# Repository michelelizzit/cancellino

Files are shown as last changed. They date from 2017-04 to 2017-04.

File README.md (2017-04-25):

# [Cancellino](https://lizzit.it/cancellino) - Open-source active-RFID automatic gate opening system
Raspberry Pi automatic RFID gate opening system with Telegram integration

    README.md
  
    Written by: Michele Lizzit <lizzit.it>, 25 Apr 2017
    Last update: 25 Apr 2017
    Version: 1.0

More informations are available on the project website: https://lizzit.it/cancellino  

## Description of the project
Cancellino is composed of some active tags and a main unit connected to the gate lock, when the main unit detects the presence of a tag in a set range (configurable from a few cm to 10m), it opens the gate.  
Cancellino does not implemet any form of encryption, the tag broadcasts a static key every two seconds, if the key is correct the main unit opens the gate. It was originally designed for applications where the security of the gate is not a concern (in my case the gate is 1m high, and can be easily opened with a piece of plastic).  
The main unit is composed of a Raspberry Pi connected to the gate lock and to an nRF24L01+ wireless module.  
Each tag is composed of a battery (CR2032), an MCU (Atmega328), and an nRF24L01+ wireless module.  

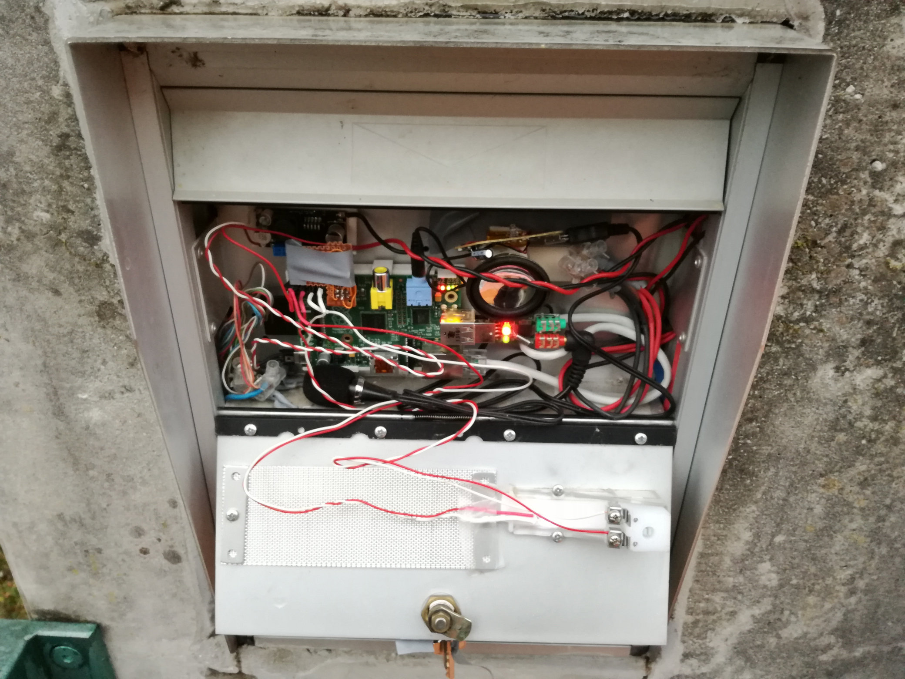
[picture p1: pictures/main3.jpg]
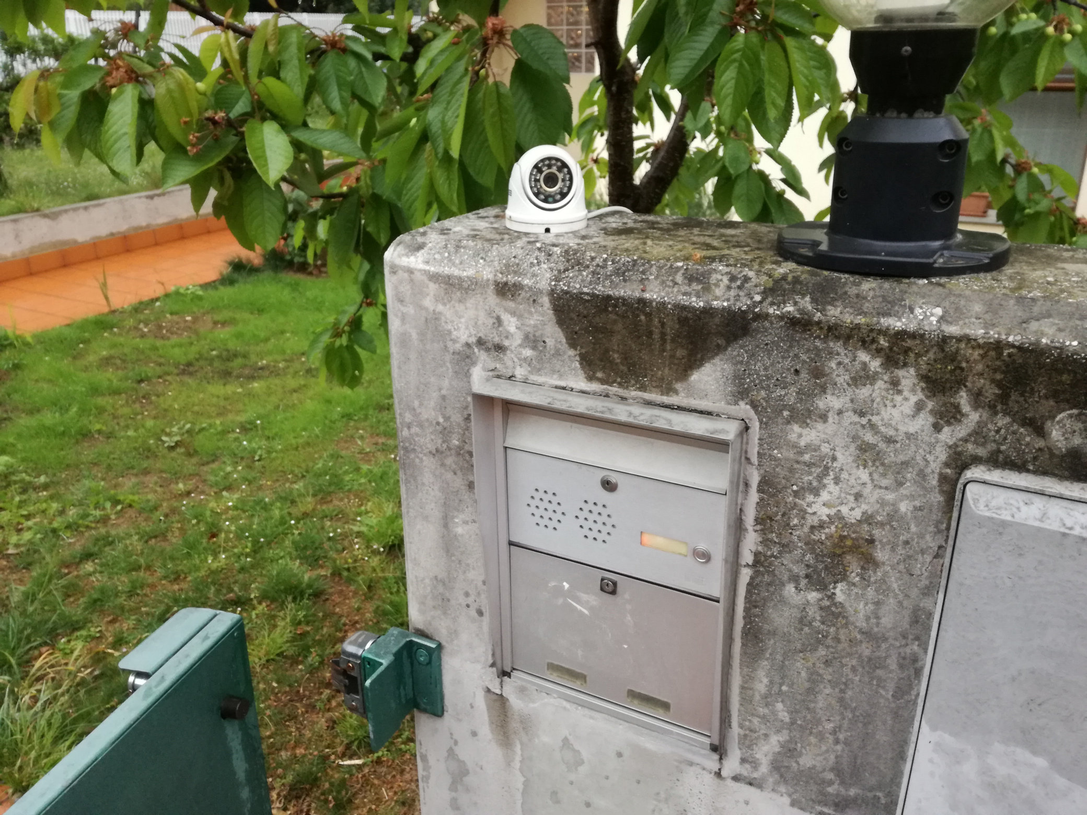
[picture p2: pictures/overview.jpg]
|  |  |
|---|---|
| The main unit in place | The gate |

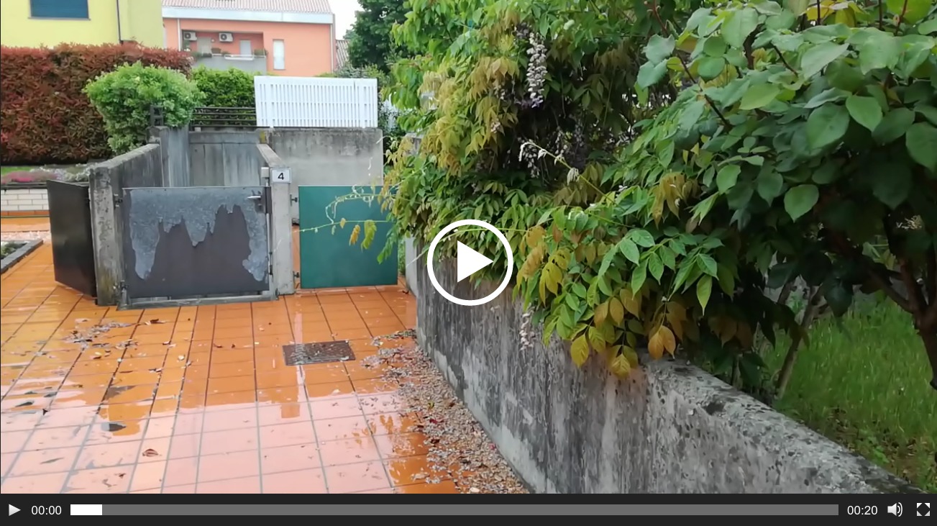
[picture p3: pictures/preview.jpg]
PREVIEW (https://lizzit.it/dl/video_cancellino.html)


## Install:

* connect the nRF24L01+ module to your RaspberryPI
* enable the SPI interface using raspi-config
* install telegram-cli and enable its daemon
* copy the folder "cancellino" to your RaspberryPI
* configure cancellino by editing "Cancello.java"
* place a script in /home/pi/open_gate_raspi.sh that opens the gate when called (usually a script that sends an high pulse on a GPIO that is connected to the lock via a solid state relay)
* configure the tag by editing Config.h
* upload the tag firmware using Arduino IDE

## Start:
```bash
javac -classpath .:classes:/opt/pi4j/lib/'*' Cancello.java;
sudo java -classpath .:classes:/opt/pi4j/lib/'*' Cancello
```
  
To automatically start the software at boot you can create an init file that executes only the last command (there is no need to compile the source code each time).  

## Tag
The tag can be built either by using the PCB or by using a prototype board, the advantage of the PCB version is its small size.  

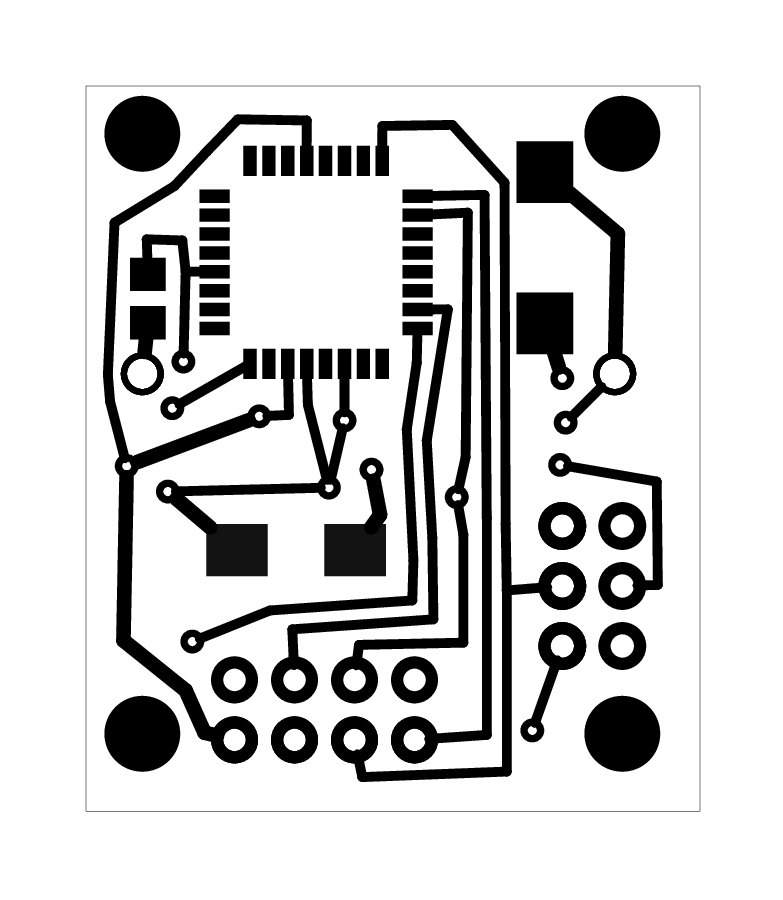
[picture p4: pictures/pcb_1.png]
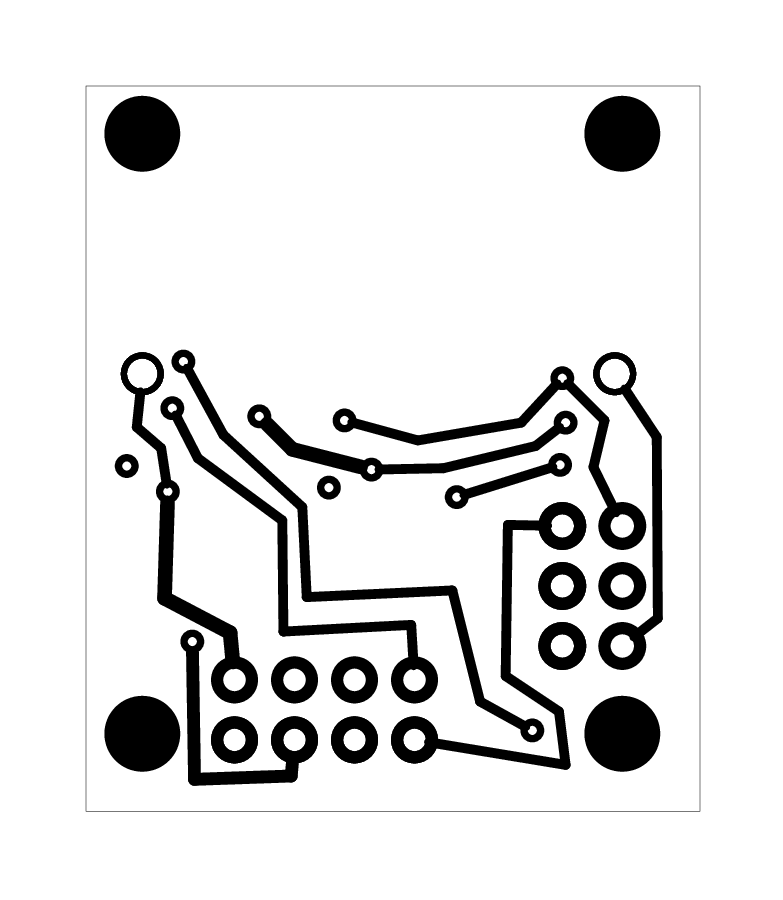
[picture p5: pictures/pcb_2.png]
|  |  |
|---|---|

The tag is powered by one CR2032 battery, with one battery the tag can work for about 6 months.  
The tag has an ICSP port which can be used to program the MCU (Atmega328P).  

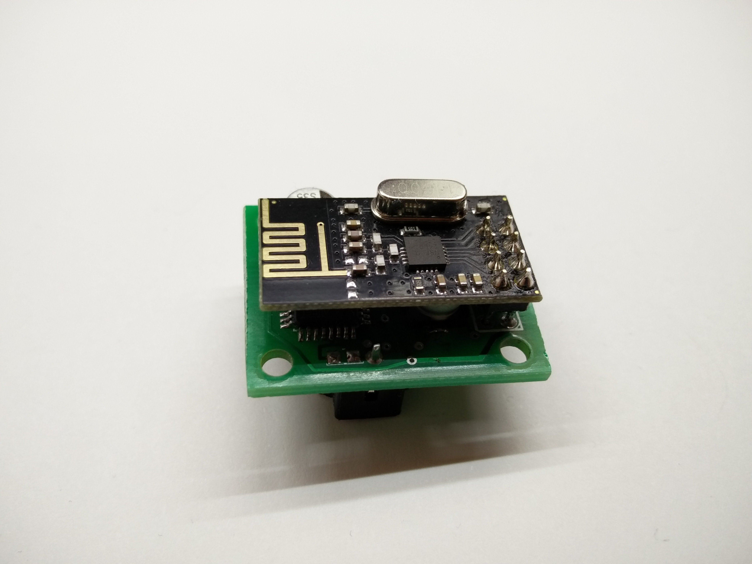
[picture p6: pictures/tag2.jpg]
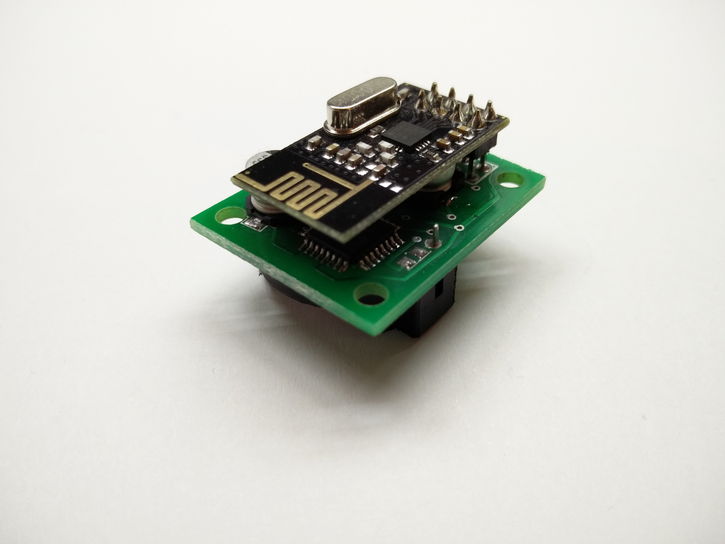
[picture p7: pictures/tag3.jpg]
|  |  |
|---|---|
| A "PCB version" tag | A "PCB version" tag |

The MCU is configured to use its internal (8MHz) oscillator in order to minimize the number of electronic components needed for a tag.  

Every two seconds the tag broadcasts a string and then puts the nRF24L01+ in "power down" mode, in this mode the nRF24L01+ draws about 100nA.  
The module draws 7.0mA while transmitting, but the total time the nRF24L01+ in not in power down mode is about 40ms every 2 seconds so the (theoretical) total power consumption is still very low.  
The actual average power consumption I measured is 50µA, which allows about 6 months of continuous operation with a single CR2032.  

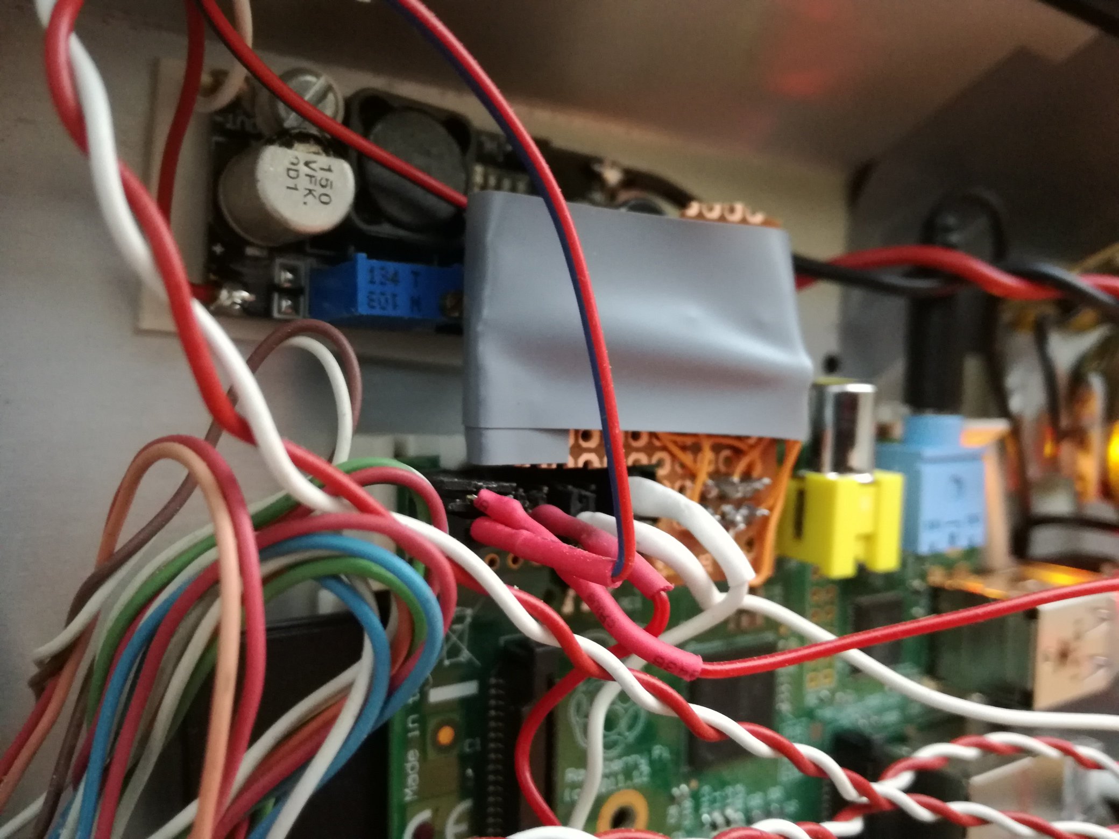
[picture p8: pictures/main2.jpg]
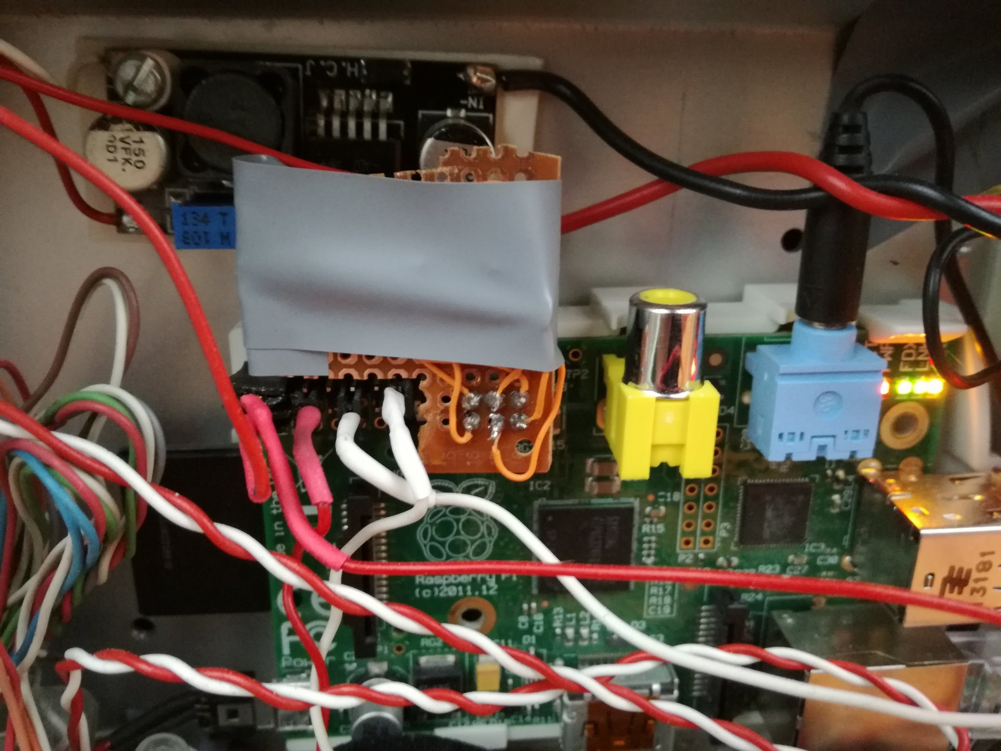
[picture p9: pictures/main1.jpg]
|  |  |
|---|---|
| The nRF24L01+ module on the main unit | The main unit |

The receiver is placed on a Raspberry Pi near the gate (I also use the Raspberry Pi as a door phone), when the Raspberry Pi receives an authorized string (which presumably comes from an authorized tag) it opens the gate, plays an audio file and sends a Telegram message containing informations on the tag (who has opened the gate).  
In a future software release I plan to implement a feature that notifies the user when the battery is low via Telegram (without requiring a hardware modification). 

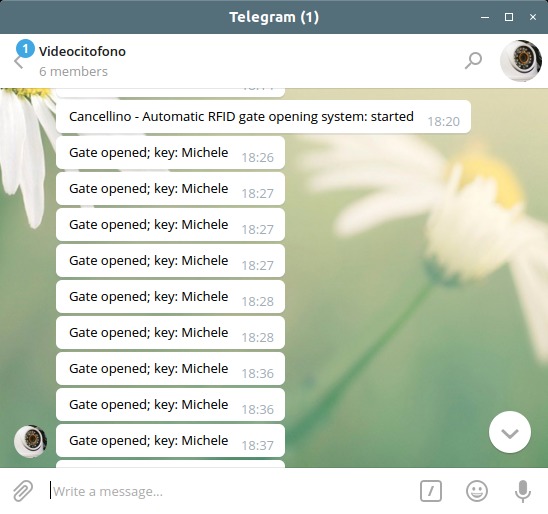
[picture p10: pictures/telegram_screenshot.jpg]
|  |
|---|
| A prototype of the tag on a perfboard in its 3D-printed case |

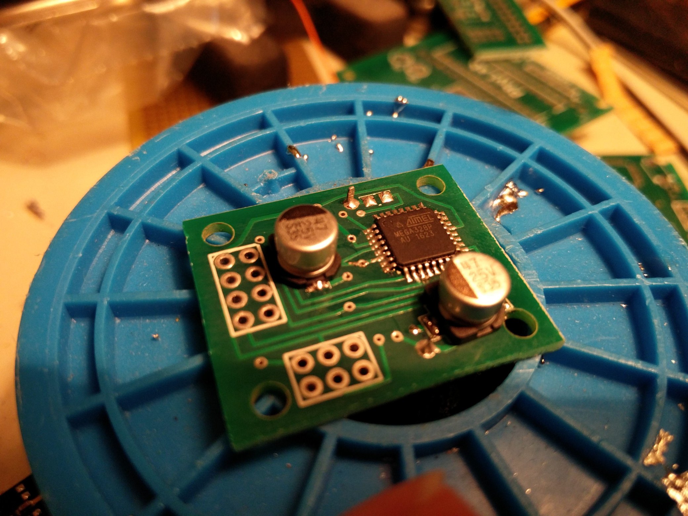
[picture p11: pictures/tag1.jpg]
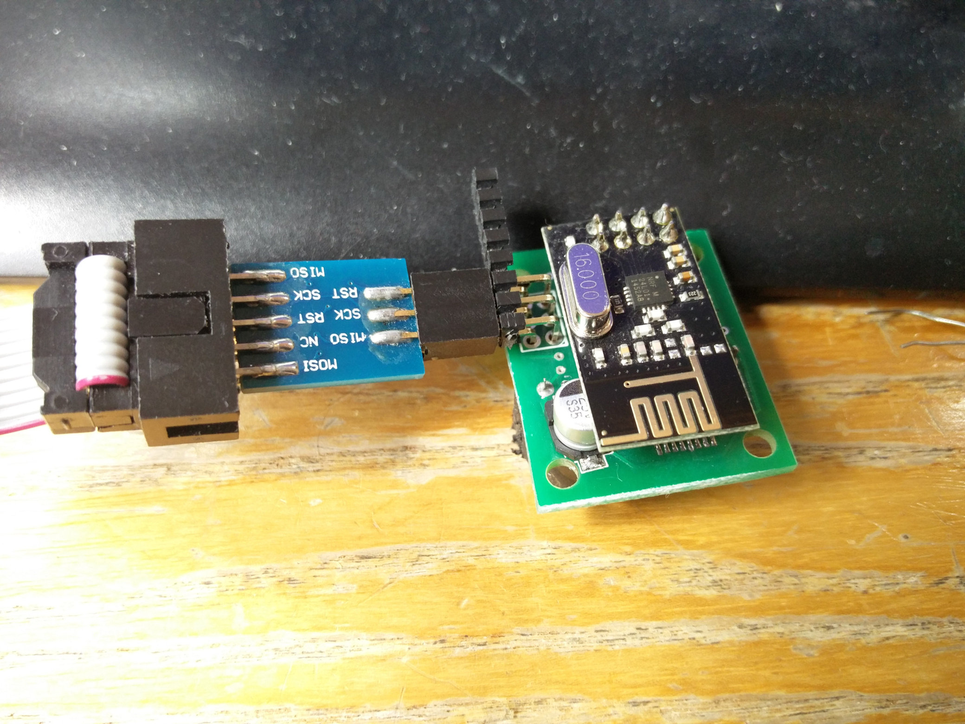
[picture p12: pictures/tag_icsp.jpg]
ICSP
|  |  |
|---|---|
| The tag before soldering the nRF24L01+ module | An AVR programmer connected to a tag via ICSP |

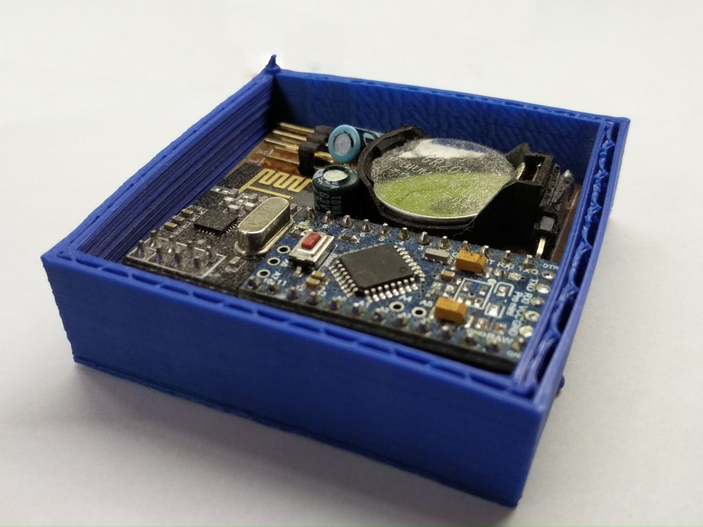
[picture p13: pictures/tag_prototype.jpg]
|  |
|---|
| A Telegram message from Cancellino |

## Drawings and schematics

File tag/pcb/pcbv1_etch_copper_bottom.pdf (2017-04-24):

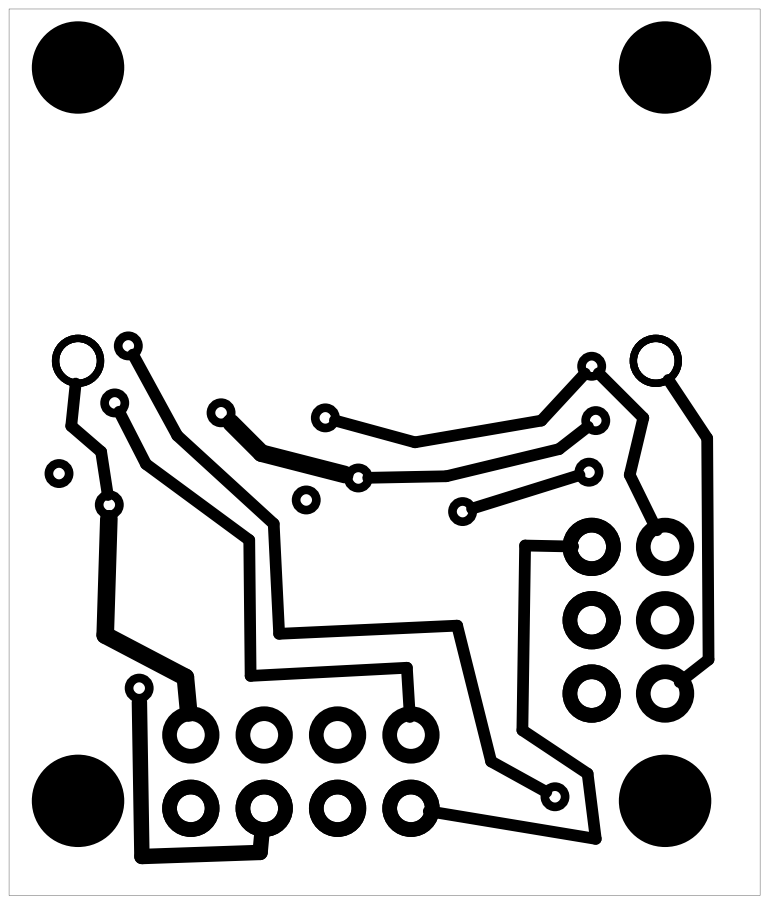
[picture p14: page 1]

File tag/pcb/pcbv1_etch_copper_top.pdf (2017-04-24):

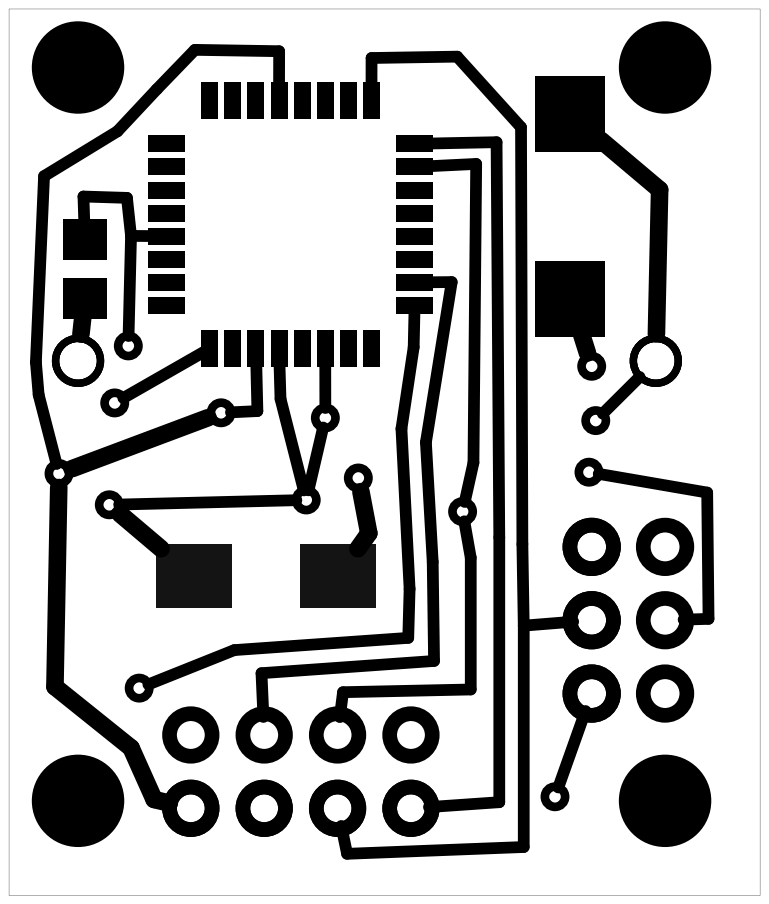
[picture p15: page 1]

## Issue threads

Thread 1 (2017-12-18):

Nullpointer exception

emperorcuzzy, 2017-12-18:
It throws up this error.

Exception in thread "main" java.lang.NullPointerException
	at cancellino.Cancello.sendTelegram(Cancello.java:84)
	at cancellino.Cancello.main(Cancello.java:31)
Java Result: 1
BUILD SUCCESSFUL (total time: 20 seconds)

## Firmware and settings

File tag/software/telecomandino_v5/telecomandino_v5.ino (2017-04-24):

/*  
 *  Cancellino - code for the RFID active tag
 *  Author: Michele Lizzit <michele@lizzit.it> - lizzit.it
 *  v1.1 - 23/4/2017
 *  
 *  Please go to https://lizzit.it/cancellino for more informations about the project
 *  
 *  
 *  Copyright (C) 2017  Michele Lizzit
 *
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
 *  You should have received a copy of the GNU Affero General Public License
 *  along with this program.  If not, see <http://www.gnu.org/licenses/>.
 */

#include "Config.h"

#include "nRF24L01_mini.h"
#include <avr/power.h>
#include <avr/sleep.h>
#include <avr/wdt.h>
#include "LowPower.h"

#ifdef DEBUG
unsigned long timeOn;
#endif

void setup() {
  //if serial debug is enabled initialize the serial port and send a character
  #ifdef DEBUG
    Serial.begin(115200);
    Serial.println("Initializing...");
    timeOn = micros();
  #endif

  delayMicroseconds(50000);
  
  initializeNRF24L01(); //initialize the nRF24L01+
  powerDownNRF(); //put the nRF24L01+ into power down mode (0.1mA power consumption)
  //powerSaveMode(); //for some strange and unknown reason uses more power instead of less

  //WARNING: if the battery is low, tension will drop and the code 
  //will hang here, resetting the MCU and triggering an infinite loop
  //that will rapidly discarge the remaining battery
  //TODO: prevent complete battery discarge

  /*powerDownNRF(); //put the nRF24L01+ into power down mode (0.1mA power consumption)
  enterSleepMode(); //put the MCU into sleep mode
  wakeUpRoutine(); //function called when exiting sleep*/

  //if debug blink is enabled set pin 13 to output
  #ifdef DEBUG_BLINK13
    pinMode(13, OUTPUT);
  #endif
}

byte authKey[] = {'P', 'L', 'U', 'T', 'O', 'N', 'I', 'U', 'M', '0'}; //the static packet to be transmitted
void loop() {
   powerUpNRF(); //power up the nRF24L01+ from "power down" state
   delayMicroseconds(150); //time required for the nRF24L01+ to start up
   sendStringNRF(authKey, 10); //transmit the 10-byte packet
   powerDownNRF(); //put the nRF24L01+ into power down mode (0.1mA power consumption)
   
   enterSleepMode(); //put the MCU into sleep mode
   //now the MCU waits 2 seconds in sleep mode
   wakeUpRoutine(); //function called when exiting sleep
   
   #ifdef DEBUG //if serial debug enabled send a char on the serial port
     Serial.println("W");
     Serial.flush();
   #endif

   #ifdef DEBUG_BLINK13 //if debug blink enabled, send a high pulse on pin 13
     digitalWrite(13, HIGH);
     delay(250);
     digitalWrite(13, LOW);
   #endif
}

void enterSleepMode() {
  //power_spi_disable();
  LowPower.powerDown(SLEEP_2S, ADC_OFF, BOD_OFF);  
  #ifdef DEBUG
    Serial.print("MCU was ACTIVE for ");
    Serial.print(micros() - timeOn);
    Serial.println(" uS");
  #endif
}

void wakeUpRoutine() {
  //power_spi_enable();  
  #ifdef DEBUG
    timeOn = micros();
  #endif
}

void powerSaveMode() {
  //disable brown out detection
  noInterrupts();
  MCUCR = bit (BODS) | bit (BODSE);
  MCUCR = bit (BODS);
  interrupts();

  //duplicate of the code above
  sleep_bod_disable(); 

  //disable ADC
  power_adc_disable();

  //disable I2C
  power_twi_disable();

  //disables some timers
  power_timer0_disable();
  power_timer1_disable();
  power_timer2_disable();
}

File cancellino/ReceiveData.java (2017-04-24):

/*
 *  nRF24L01+ Java library for RaspberryPi - adapted version for "cancellino"
 *  Author: Michele Lizzit <michele@lizzit.it> - lizzit.it
 *  v1.1 - 23/4/2017
 *
 *  Please go to https://lizzit.it/cancellino for more informations about the project
 *
 *
 *  Copyright (C) 2017  Michele Lizzit
 *
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
 *  You should have received a copy of the GNU Affero General Public License
 *  along with this program.  If not, see <http://www.gnu.org/licenses/>.
 */

import com.pi4j.io.gpio.GpioController;
import com.pi4j.io.gpio.GpioFactory;
import com.pi4j.io.gpio.GpioPinDigitalOutput;
import com.pi4j.io.gpio.RaspiPin;
import com.pi4j.io.spi.SpiChannel;
import com.pi4j.io.spi.SpiDevice;
import com.pi4j.io.spi.SpiFactory;
import java.io.*;

public class ReceiveData {

	public static SpiDevice spi = null;
	private byte WRITE_CMD = 0x40;
	private byte READ_CMD  = 0x41;
	final GpioController gpio = GpioFactory.getInstance();
	final GpioPinDigitalOutput CE_nRF24L01 = gpio.provisionDigitalOutputPin(RaspiPin.GPIO_06); //utilizza la numerazione wiringPI che e' molto strana

	@SuppressWarnings("unused")
	public void start() {
		try {
			spi = SpiFactory.getInstance(SpiChannel.CS0,
					500000,//SpiDevice.DEFAULT_SPI_SPEED, // default spi speed 1 MHz
					SpiDevice.DEFAULT_SPI_MODE); // default spi mode 0
		} catch (IOException e) {
			e.printStackTrace();
		}
		CE_nRF24L01.low();
		initializeNRF24L01();
		setRXMode();
		CE_nRF24L01.high();
	}

	//Commands
	final byte R_REG = (byte)0x00;
	final byte W_REG = (byte)0x20;
	final byte RX_PAYLOAD = (byte)0x61;
	final byte TX_PAYLOAD = (byte)0xA0;
	final byte FLUSH_TX = (byte)0xE1;
	final byte FLUSH_RX = (byte)0xE2;
	final byte ACTIVATE = (byte)0x50;
	final byte R_STATUS = (byte)0xFF;

	//Registers
	final byte CONFIG = (byte)0x00;
	final byte EN_AA = (byte)0x01;
	final byte EN_RXADDR = (byte)0x02;
	final byte SETUP_AW = (byte)0x03;
	final byte SETUP_RETR = (byte)0x04;
	final byte RF_CH = (byte)0x05;
	final byte RF_SETUP = (byte)0x06;
	public final byte STATUS = (byte)0x07;
	final byte OBSERVE_TX = (byte)0x08;
	final byte CD = (byte)0x09;
	final byte RX_ADDR_P0 = (byte)0x0A;
	final byte RX_ADDR_P1 = (byte)0x0B;
	final byte RX_ADDR_P2 = (byte)0x0C;
	final byte RX_ADDR_P3 = (byte)0x0D;
	final byte RX_ADDR_P4 = (byte)0x0E;
	final byte RX_ADDR_P5 = (byte)0x0F;
	final byte TX_ADDR = (byte)0x10;
	final byte RX_PW_P0 = (byte)0x11;
	final byte RX_PW_P1 = (byte)0x12;
	final byte RX_PW_P2 = (byte)0x13;
	final byte RX_PW_P3 = (byte)0x14;
	final byte RX_PW_P4 = (byte)0x15;
	final byte RX_PW_P5 = (byte)0x16;
	final byte FIFO_STATUS = (byte)0x17;
	final byte DYNPD = (byte)0x1C;
	final byte FEATURE = (byte)0x1D;

	//Data
	private final byte[] RXTX_ADDR = { (byte)0x87, (byte)0xC1, (byte)0xB9 }; //Randomly chosen address

	public void initializeNRF24L01() {
		setCsnPin(true);
		CE_nRF24L01.low();

		// wait for the nRF24L01 to set up
		try { Thread.sleep(20); }
		catch (InterruptedException e) { e.printStackTrace(); }
		regWrite(CONFIG, (byte)0x0B); //RX mode
		regWrite(EN_AA, (byte)0x00);
		regWrite(EN_RXADDR, (byte)0x01);
		regWrite(SETUP_AW, (byte)0x01);
		regWrite(SETUP_RETR, (byte)0x00);
		regWrite(RF_CH, (byte)0x01); //RADIO CHANNEL
		regWrite(RF_SETUP, (byte)0x26); //250kbps, 0dBm = 0x26 250kbps, 0dBm (1mW) = 0x06
		regWrite(RX_PW_P0, (byte)0x0A); //Payload size = 10 byte

		addrWrite(RX_ADDR_P0, (byte)3, RXTX_ADDR);
		addrWrite(TX_ADDR, (byte)3, RXTX_ADDR);

		//System.out.println(ReadRegister(TX_ADDR));

		flushBuffers();

		// wait for the nRF24L01 to set up
		try { Thread.sleep(2); }
		catch (InterruptedException e) { e.printStackTrace(); }
		System.out.println("Initialized");
	}

	public void setRXMode() {
		regWrite(CONFIG, (byte)0x0B);
		CE_nRF24L01.high();
	}

	private void setTXMode() {
		CE_nRF24L01.low();
		regWrite(CONFIG, (byte)0x0A);

		CE_nRF24L01.high();
		long currentTime = System.nanoTime();
		while (System.nanoTime() - currentTime < 15000) {

		}
		CE_nRF24L01.low();
	}

	private void powerDownNRF() {
		CE_nRF24L01.low();
		regWrite(CONFIG, (byte)0);
	}

	public String getPacket() {
		byte[] data = new byte[10];
		getPayload((byte)10, data);

		regWrite(STATUS, (byte)0x40);
		return new String(data);
	}

	public byte signalStrength() {
		return regRead(CD);
	}

	public void setPayloadContent(String payload) {
		setCsnPin(false);
		byte packet[] = new byte[payload.length() + 1];
		packet[0] = TX_PAYLOAD;

		for (int cnt = 0; cnt < payload.length(); cnt++)
			packet[cnt + 1] = ((byte)payload.charAt(cnt));

		try {spi.write(packet);}catch (IOException e) {e.printStackTrace();}
		setCsnPin(true);
	}

	public void sendStringNRF(String packet) {
		setPayloadContent(packet);

		setTXMode();
		byte stat;
		do {
			stat = regRead(STATUS);
			//System.out.println(Integer.toBinaryString(stat));
			//try {Thread.sleep(1);} catch (InterruptedException e) {e.printStackTrace();}
		} while ((stat & 0x20) == 0);
		//System.out.println("SENT");

		regWrite(STATUS, (byte)0x20);
		setRXMode();
	}

	public boolean packetAvail() {
		byte stat = regRead(STATUS);
		//System.out.println(Integer.toBinaryString(stat));
		return (stat & 0x40) != 0;
	}

	public void printRegisters() {
		for (byte i=0; i<29; i++) {
			setCsnPin(false);

			//System.out.println(transfer((byte)(i)));
			byte packet[] = new byte[2];
			packet[0] = i;
			packet[1] = 0x00;
			byte[] result = new byte[2];
			try {result = spi.write(packet);}catch (IOException e) {e.printStackTrace();}
			//byte result = packet[1];

			//byte result = transfer((byte)0x00);
			setCsnPin(true);
			System.out.print("reg ");
			System.out.print(i);
			System.out.print(": ");
			//System.out.print(Integer.toBinaryString(result));
			System.out.println(Integer.toBinaryString( (result[1]) ));
		}
	}

	public void flushBuffers() {
		regWrite(STATUS, (byte)0x70);
		sendCommand(FLUSH_RX);
		sendCommand(FLUSH_TX);
	}

	private void regWrite(byte reg, byte val) {
		setCsnPin(false);
		byte packet[] = new byte[2];
		packet[0] = (byte)(W_REG | reg);
		packet[1] = val;
		try {spi.write(packet);}catch (IOException e) {e.printStackTrace();}
		setCsnPin(true);
	}

	private void addrWrite(byte regNum, byte len, byte[] address) {
		setCsnPin(false);
		byte packet[] = new byte[len + 1];
		packet[0] = (byte)(W_REG | regNum);

		for (int cnt = 0; cnt < len; cnt++)
			packet[cnt + 1] = ((byte)address[cnt]);

		try {spi.write(packet);}catch (IOException e) {e.printStackTrace();}
		setCsnPin(true);
	}

	public byte regRead(byte regNum) {
		setCsnPin(false);
		byte packet[] = new byte[2];
		packet[0] = regNum;
		packet[1] = 0x00;
		byte[] result = new byte[2];
		try {result = spi.write(packet);}catch (IOException e) {e.printStackTrace();}
		setCsnPin(true);
		return result[1];
	}

	private void sendCommand(byte command) {
		setCsnPin(false);
		byte packet[] = new byte[1];
		packet[0] = command;
		try {spi.write(packet);}catch (IOException e) {e.printStackTrace();}
		setCsnPin(true);
	}
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

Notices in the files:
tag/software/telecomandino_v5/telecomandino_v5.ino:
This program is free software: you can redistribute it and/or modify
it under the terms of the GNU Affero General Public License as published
